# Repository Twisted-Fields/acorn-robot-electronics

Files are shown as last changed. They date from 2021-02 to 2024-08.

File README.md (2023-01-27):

# Acorn Robot Electronics

### About

PCBs designed in Kicad for Acorn the farming robot.

Our dream is that you will fab your own boards, make changes, and share your work - giving this design life beyond our efforts.

Designed by Taylor Alexander for Twisted Fields, for the Acorn Precision Farming Rover.

Many thanks to [Daniel Theobald](https://www.twistedfields.com/blog). Without your financial support and encouragement this project would not have been possible.

Thanks to all of our supporters on Open Collective. Your contributions are helping grow this project in to a sustainable open source organization.

You can support this project yourself at our [Open Collective Page](https://opencollective.com/twisted-fields-research-collective).

To learn more about Acorn, please see our [announcement blog post](https://community.twistedfields.com/t/introducing-acorn-a-precision-farming-rover-from-twisted-fields/).
Or see a more recent [technical update here](https://community.twistedfields.com/t/march-2022-update-simulation-brakes-funding-and-navigation-improvements/202).

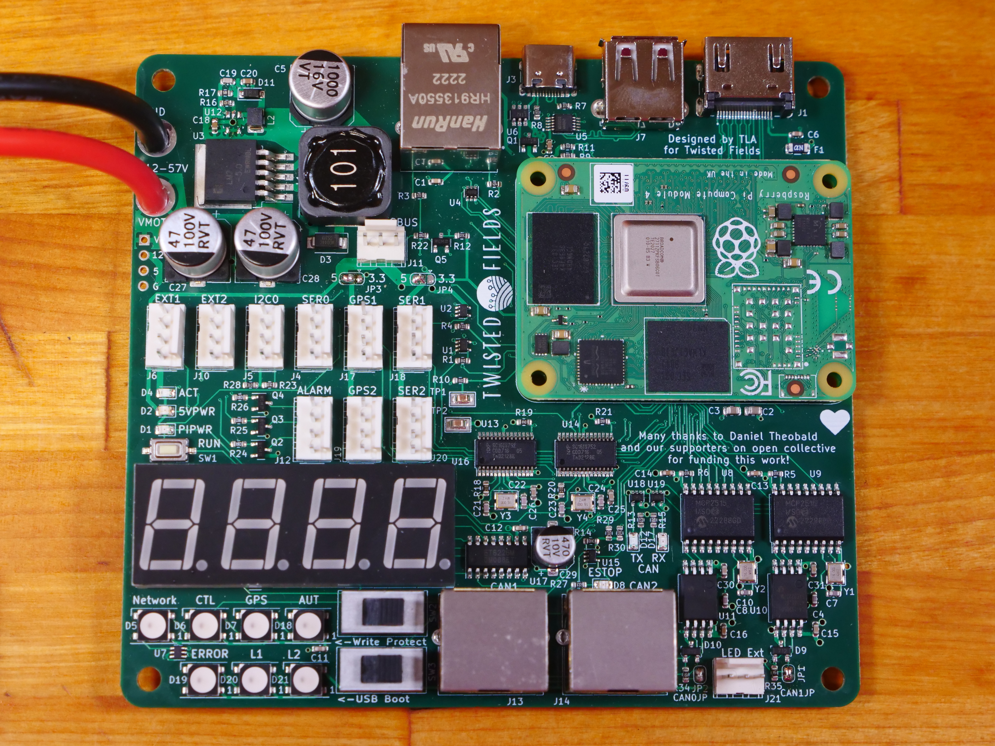
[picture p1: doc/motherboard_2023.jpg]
A photo of the CM4 motherboard


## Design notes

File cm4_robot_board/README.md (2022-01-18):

# Acorn Raspberry Pi Motherboard

### About

This is the motherboard design used on Acorn, the precision farming rover
from Twisted Fields.

This board provides motor control communication to four Odrive motor controllers
via RS-485, e-stop control, motor power control, and more.

For more information please see http://community.twistedfields.com

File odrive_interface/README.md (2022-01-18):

# Acorn Odrive Interface Board

### About

This board attaches to the odrive motor controller and provides
an interface for RS-485 and emergency stop over ethernet cabling.

It also provides connections to a few sensors, and includes
relays for emergency braking.

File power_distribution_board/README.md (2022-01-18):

# Acorn Power Distribution Board

### About

This board attaches to the Acorn motherboard and handles
switching of the high current power going to the motors.

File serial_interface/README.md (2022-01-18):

# Acorn Serial interface board

### About

This board attaches to any raspberry pi 40 pin header
or to the special 40 pin header on our robot motherboard
and provides connections for opto-isolated RS-485 serial
as well as emergency stop connections, designed to
mate with our Odrive interface board.

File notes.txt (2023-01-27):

TODO RECOMMENDATIONS AFTER PRODUCTION

Make clear the polarity for U5 、D19、D5、D6、D20、D7、D21、D18

e-stop should activate if a cable is disconnected. - nevermind, it does this

make CAN controller crystal value more clear - 16mhz not 12mhz!

invert CAN TX/RX LED polarity either by using inverting buffer part number or by rewiring input - maybe inverted is best for fast cut-off?

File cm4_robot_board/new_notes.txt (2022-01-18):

WL_nDisable logic high indicates the enable/disable state of wireless networking. may want to connect it to an LED. can also be pulled low to disable wlan
BT_nDisable same as above for bluetooth

etherney jack for rpi networking
https://www.digikey.com/en/products/detail/bel-fuse-inc/0826-1X1T-GH-F/2257874

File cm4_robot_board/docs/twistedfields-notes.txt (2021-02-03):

CCG304805S or PDQ30-Q48-S5-D for 5v power supply

SC16IS762 in SPI mode for dual serial ports
See this for some background on enabling kernel support.
https://www.raspberrypi.org/forums/viewtopic.php?f=107&t=146908&start=25
Read both pages but check if newer kernels still need this.

Possibly ISL83488 or 65HVD32 or THVD1451 for rs485 line drivers. prefer THVD1451, must double check datasheets if others used.
will use kicad footprint of THVD1451 but may prefer ISL83488 for slew rate limited drivers.
should use 250kbps data rate or lower
See layout guidelines at http://www.ti.com/lit/ds/symlink/thvd1451.pdf

See https://www.waveshare.com/wiki/2-CH_RS485_HAT for some details

Can draw up to 500ma from the 3.3v line on the raspberry pi.
https://pinout.xyz/pinout/pin1_3v3_power

Should add a connector for SPI e-ink display.
https://www.waveshare.com/wiki/7.5inch_e-Paper_HAT_(B)

ABM3C-14.7456MHZ-D4Y-T  for serial crystal

BTS500851TMAATMA1 for power switch.

zener  	MMSZ5226B-7-F 

Power Capacitors
565-4013-ND 
EKYB101ELL101MJ20S 

Inductor
RLB0913-470K-ND 
RLB0913-470K 

THVD1451 RS485 tranceiver

TVS Diodes:
SM712-TP or
SM712-02HTG 

Solar current sensor:
unidirectional 10A
ACS725LLCTR-10AU-T

Bidirectional 5A:
ACS722LLCTR-05AB-T

Bidirectional 10A:
ACS722LLCTR-10AB-T

Slide switchs should be:
ASE1D-2M-10-Z
Kicad lists another part for the footprint, but they match. This part is 60v tolerant.

SPST switch:
GF-123-0054

alarm
TXL7-V96-930-S

Molex connectors for keypad:
0022232051 

inductor:
MLZ2012N100LT000

5v external power supplies for Jetson Nano:
$108 compact 100w:
https://www.digikey.com/product-detail/en/cui-inc/PQA50-D48-S5-T/102-3295-ND/4765796
$39 60w no remote on/off (can drive from switched 48v):
https://www.digikey.com/product-detail/en/mean-well-usa-inc/RSD-60L-5/1866-5467-ND/7706269
$40 compact 30w:
https://www.digikey.com/product-detail/en/cui-inc/PYBE30-Q48-S5-DIN/102-6035-ND/9859991

e-paper screen wiring:
https://www.waveshare.com/wiki/7.5inch_e-Paper_HAT_(B)

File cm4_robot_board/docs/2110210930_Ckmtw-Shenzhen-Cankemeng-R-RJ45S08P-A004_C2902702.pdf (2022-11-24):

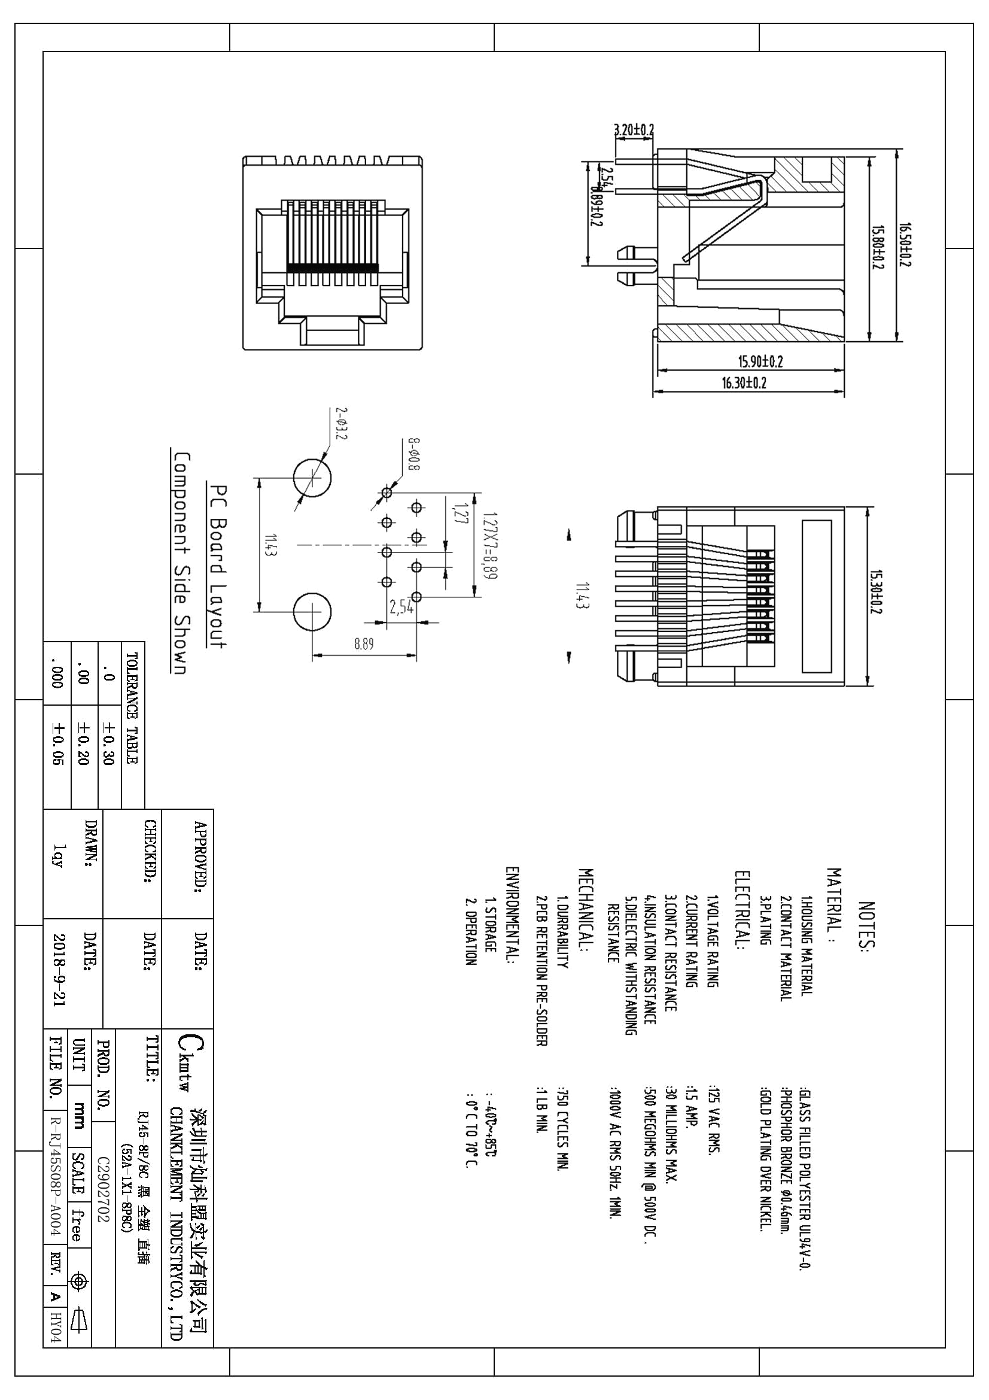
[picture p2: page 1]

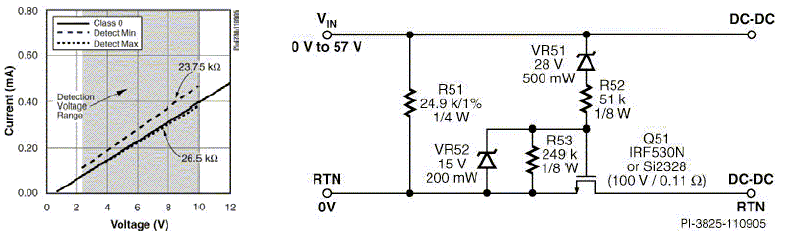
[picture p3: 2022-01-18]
cm4_robot_board/docs/poe/class_0_via_eetimes.gif

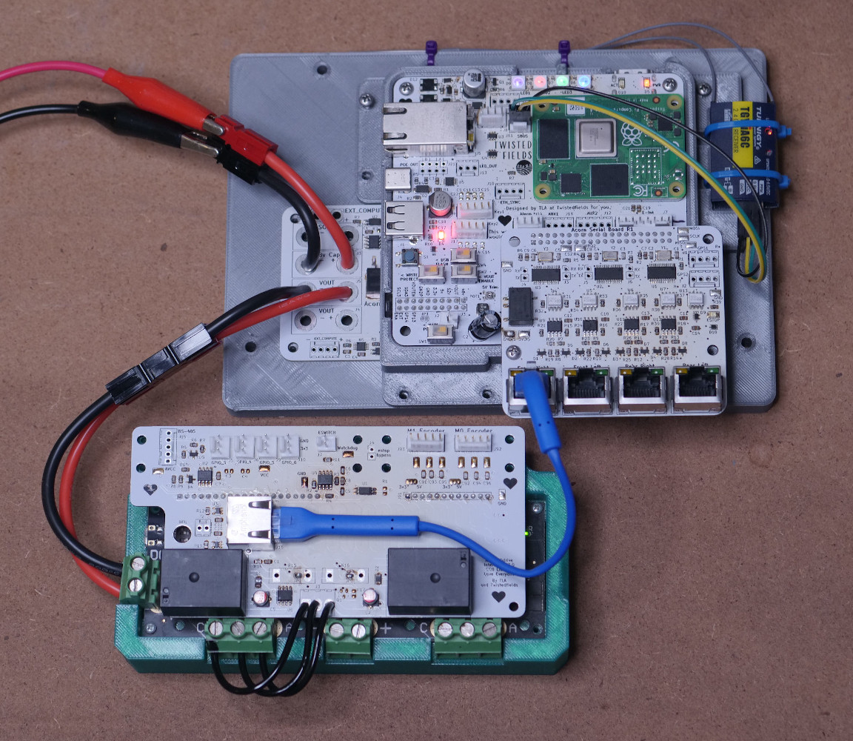
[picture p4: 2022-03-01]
doc/motherboard_all.jpg

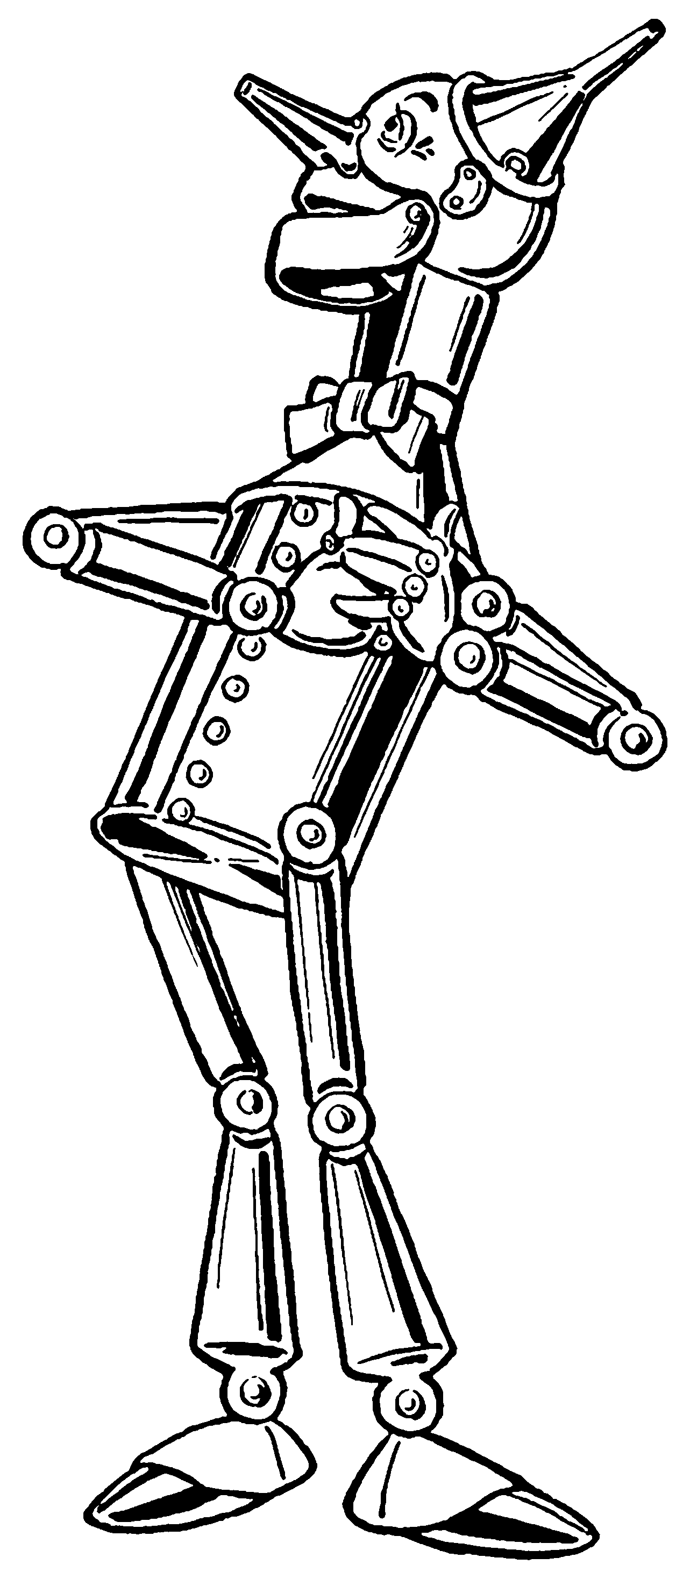
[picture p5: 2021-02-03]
cm4_robot_board/artwork/Tin_Woodman.png

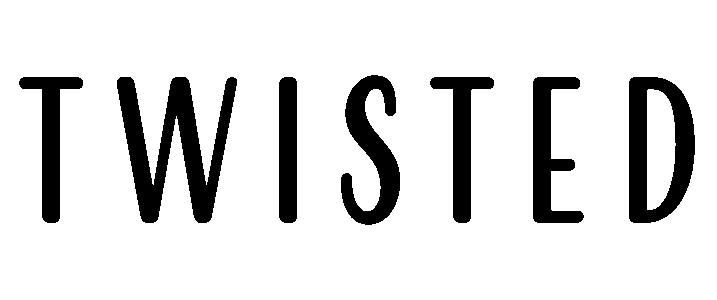
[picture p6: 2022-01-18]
cm4_robot_board/artwork/twisted.png

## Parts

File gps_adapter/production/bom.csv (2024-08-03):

Designator | Footprint | Quantity | Value | LCSC Part #
H1, H2, H3, H4 | MountingHole_3.7mm | 4 | MountingHole
J3 | PinHeader_2x05_P2.54mm_Vertical | 1 | Serial Input
JP1, JP2 | SolderJumper-2_P1.3mm_Open_RoundedPad1.0x1.5mm | 2 | SolderJumper_2_Open
U1, U2 | GPS-RTK-SMA | 2 | GPS-RTK-SMA

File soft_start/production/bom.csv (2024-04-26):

Designator | Footprint | Quantity | Value | LCSC Part #
C1, C2 | 0603 | 2 | 20p | C1648
C14, C15, C29, C30, C31, C33, C34, C35, C36, C37, C4 | 0603 | 11 | 100n | C14663
C16, C32 | 0603 | 2 | 1u | C15849
C3 | 0805 | 1 | 10u | C15850
C5, C7 | 1210 | 2 | 4.7uF 100V | C342614
C6 | CP_Elec_8x10.5 | 1 | 47uF 63V solid | C5246568
D1 | D_SMA | 1 | SS310 | C15874
D2, D33 | D_SOD-323 | 2 | Zener 10v | C85383
D28, D29 | D_SOD-323 | 2 | 1N4148WS | C2128
J2 | Ckmtw-W-2510S06P_1x06_P2.54mm_Vertical | 1 | Conn_01x06 | C140771
J3 | PowerPole_PP45_1336G1_1x2_Horizontal | 1 | Power Output
J4, J5 | PowerPole_PP45_1336G1_1x2_Horizontal | 2 | Conn_01x02
L3 | L_Chilisin_BMRB00060612 | 1 | 47uH | C5189962
Q1, Q2 | SOT-23 | 2 | Q_NMOS_GSD | C2891566
Q3, Q4, Q5, Q6 | TO-252-2 | 4 | 100V 34A PMOS | C2758447
R1, R2 | 1206 | 2 | 10k | C3013377
R13, R15 | 2512 | 2 | 3mΩ | C2688862
R3, R40 | 2512 | 2 | 2k 2 watt | C175463
R34, R35, R37, R38 | 0603 | 4 | 50k 0.1% | C304067
R36, R39 | 0603 | 2 | 5.1k 0.1% | C122969
R8 | 0603 | 1 | 1.1k | C22764
TP1 | TestPoint_Loop_D2.60mm_Drill1.6mm_Beaded | 1 | TestPoint | C5199814
U1 | SOT-23-6 | 1 | USBLC6-4SC6 | C558419
U2 | SOIC-8_5.23x5.23mm_P1.27mm | 1 | W25Q128JVSIQ | C113767
U3 | SOT-223-3_TabPin2 | 1 | LD1117S33TR_SOT223 | C2845050
U4 | RP2040-QFN-56 | 1 | RP2040 | C2040
U7 | SOT-23-6 | 1 | INA181A2 | C2058784
Y1 | Crystal_SMD_3225-4Pin_3.2x2.5mm | 1 | 12MHz | C9002

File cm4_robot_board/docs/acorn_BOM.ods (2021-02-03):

Reference | Quantity | Value | Digikey | Footprint | Datasheet | Field4 | Field5 | Category | DK_Datasheet_Link | DK_Detail_Page | Description | Family | MPN | Manufacturer | Status | Digi-Key_PN | Field6
C18 | 1 | 1000pF | 311-1469-1-ND | Capacitor_SMD:C_0805_2012Metric | ~
C2 C1 C9 C8 | 4 | 18pF | 311-1102-1-ND | Capacitor_SMD:C_0805_2012Metric | ~
C20 | 1 | 0.15uF | 311-3393-1-ND | Capacitor_SMD:C_0805_2012Metric | ~
C27 C25 C23 C21 C28 C26 C24 C22 | 8 | DNP |  | Capacitor_SMD:C_0805_2012Metric | ~
C3 | 1 | 1uF 100v | 490-10918-1-ND | Capacitor_SMD:C_0805_2012Metric | ~
C4 | 1 | CP | 565-4013-ND | Capacitor_THT:CP_Radial_D10.0mm_P5.00mm | ~
C5 C7 C6 C13 C16 C15 C11 C12 C17 C19 C14 C10 | 12 | 0.1uF | 311-1361-1-ND | Capacitor_SMD:C_0805_2012Metric | ~
C99 | 1 | 150pF | 399-8024-1-ND | Capacitor_SMD:C_0805_2012Metric | ~
D1 D3 D14 D16 | 4 | LED_GREEN | 404-1046-1-ND | LED_SMD:LED_1206_3216Metric | ~
D12 D10 D13 D11 D23 D21 D24 D22 | 8 | CDSOT23-SM712 | CDSOT23-SM712CT-ND | digikey-footprints:SOT-23-3 | https://www.bourns.com/docs/Product-Datasheets/CDSOT23-SM712.pdf
D18 D25 D20 D19 | 4 | 3.3v Zener | MMSZ5226B-FDITR-ND | Diode_SMD:D_SOD-123 | ~
D2 D4 D15 D17 | 4 | LED_ORANGE | 404-1234-1-ND | LED_SMD:LED_1206_3216Metric | ~
D26 | 1 | LED | 160-1643-1-ND | LED_SMD:LED_1206_3216Metric | ~
D7 D6 D5 | 3 | D | MMSD4148T1GOSCT-ND | Diode_SMD:D_SOD-123 | ~
D8 | 1 | 12v Zener | MMSZ5242B-TPMSCT-ND | Diode_SMD:D_SOD-123 | ~
D9 | 1 | LED_RED | 404-1042-1-ND | LED_SMD:LED_1206_3216Metric | ~
H1 H3 H4 H2 | 4 | MountingHole |  | MountingHole:MountingHole_3.7mm | ~
J10 | 1 | Raspberry Pi | 1690-RASPBERRYPI4B/4GB-ND | Connector_PinHeader_2.54mm:PinHeader_2x20_P2.54mm_Vertical
J11 | 1 | Conn_01x06 |  | Connector_PinHeader_2.54mm:PinHeader_1x06_P2.54mm_Vertical | ~
J13 J14 J26 J27 J23 | 5 | Conn_01x05 | 455-1707-ND | Connector_JST:JST_PH_B5B-PH-K_1x05_P2.00mm_Vertical | ~ |  |  | Discrete Semiconductor Products | https://www.onsemi.com/pub/Collateral/NDS7002A-D.PDF | /product-detail/en/on-semiconductor/2N7002/2N7002NCT-ND/244664 | MOSFET N-CH 60V 115MA SOT-23 | Transistors - FETs, MOSFETs - Single | 2N7002 | ON Semiconductor | Active
J16 | 1 | Conn_01x08 | 455-1710-ND | Connector_JST:JST_PH_B8B-PH-K_1x08_P2.00mm_Vertical | ~ |  |  | Circuit Protection | https://www.bourns.com/docs/Product-Datasheets/CDSOT23-SM712.pdf | /product-detail/en/bourns-inc/CDSOT23-SM712/CDSOT23-SM712CT-ND/1630607 | TVS DIODE 7V/12V 14V/26V SOT23-3 | TVS - Diodes | CDSOT23-SM712 | Bourns Inc. | Active
J19 J25 J12 J15 J30 J18 | 6 | Conn_01x04 | 455-1706-ND | Connector_JST:JST_PH_B4B-PH-K_1x04_P2.00mm_Vertical | ~ |  |  | Discrete Semiconductor Products | http://aosmd.com/res/data_sheets/AO3401A.pdf | /product-detail/en/alpha-omega-semiconductor-inc/AO3401A/785-1001-1-ND/1855943 | MOSFET P-CH 30V 4A SOT23 | Transistors - FETs, MOSFETs - Single | AO3401A | Alpha & Omega Semiconductor Inc. | Active
J20 J24 | 2 | Conn_01x03 | 455-1705-ND | Connector_JST:JST_PH_B3B-PH-K_1x03_P2.00mm_Vertical | ~
J28 J29 | 2 | Conn_01x05 | WM4203-ND | Connector_Molex:Molex_KK-254_AE-6410-05A_1x05_P2.54mm_Vertical | 22232051 |  |  | Potentiometers, Variable Resistors | https://www.bourns.com/docs/Product-Datasheets/TC33.pdf | /product-detail/en/bourns-inc/TC33X-2-103E/TC33X-103ETR-ND/612858 | TRIMMER 10K OHM 0.1W J LEAD TOP | Trimmer Potentiometers | TC33X-2-103E | Bourns Inc. | Active
J3 J2 | 2 | Conn_01x02 | 455-1704-ND | Connector_JST:JST_PH_B2B-PH-K_1x02_P2.00mm_Vertical | ~
J32 | 1 | Conn_01x02 | 455-1611-ND | Connector_JST:JST_EH_B2B-EH-A_1x02_P2.50mm_Vertical | ~
J4 J5 J6 J1 | 4 | Conn_01x02 |  | twisted_library:BigWirePads | ~
J9 J21 J22 J8 J7 J17 J31 | 7 | Conn_01x02 |  | Connector_PinHeader_2.54mm:PinHeader_1x02_P2.54mm_Vertical | ~
L1 | 1 | L | RLB0913-470K-ND | Inductor_THT:L_Radial_D8.7mm_P5.00mm_Fastron_07HCP | ~
L2 | 1 | 10uH | 445-6762-1-ND | Inductor_SMD:L_0805_2012Metric | MLZ2012N100LT000
POT1 | 1 | TC33X-2-103E | TC33X-103ETR-ND | digikey-footprints:Trimpot_3.8mmx3.6mm_TC33X-2-103E | https://www.bourns.com/docs/Product-Datasheets/TC33.pdf
PS1 | 1 | SPBW06F-12 | 1866-4811-ND | library:CONV_SPBW06F-12 | Manufacturer Recommendations
Q12 | 1 | AO3401A | FDN352APCT-ND | digikey-footprints:SOT-23-3 | http://aosmd.com/res/data_sheets/AO3401A.pdf
Q3 Q13 Q10 Q8 Q7 Q6 Q1 Q2 Q11 Q9 Q4 | 11 | 2N7002 | 2N7002NCT-ND | digikey-footprints:SOT-23-3 | https://www.onsemi.com/pub/Collateral/NDS7002A-D.PDF | CUI Inc | Manufacturer Recommendations
Q5 | 1 | FDMS8050 | BSC030N08NS5ATMA1CT-ND | Package_TO_SOT_SMD:TDSON-8-1 | https://www.fairchildsemi.com/datasheets/FD/FDMS8050.pdf | MEANWELL | 11.1mm |  |  |  |  |  |  |  |  |  | N/A
R11 R69 R72 R56 R39 R37 R1 R10 R12 R73 R70 R68 R29 R27 | 14 | 100R | 311-100CRCT-ND | Resistor_SMD:R_0805_2012Metric | ~
R13 R41 | 2 | 330R | A106061CT-ND | Resistor_SMD:R_0805_2012Metric | ~
R14 R74 | 2 | 220R | A129741CT-ND | Resistor_SMD:R_0805_2012Metric | ~
R15 R22 R17 R25 R44 R51 R46 R54 | 8 | 130R | RMCF0805FT130RCT-ND | Resistor_SMD:R_0805_2012Metric | ~
R19 R16 R21 R23 R20 R18 R24 R26 R48 R45 R50 R52 R49 R47 R53 R55 | 16 | 750R | RMCF0805FT750RCT-ND | Resistor_SMD:R_0805_2012Metric | ~
R2 R3 R4 R5 R30 R31 R32 R33 | 8 | 499R | 311-499CRCT-ND | Resistor_SMD:R_0805_2012Metric | ~
R36 | 1 | 10K | 311-10.0KCRCT-ND | Resistor_SMD:R_0805_2012Metric | ~
R42 | 1 | 44.2k 0.1% | P44.2KDACT-ND | Resistor_SMD:R_0805_2012Metric | ~
R43 R61 | 2 | 10.2k 0.1% | P10.2KDACT-ND | Resistor_SMD:R_0805_2012Metric | ~
R58 | 1 | DNP |  | Resistor_SMD:R_0805_2012Metric | ~
R60 R65 | 2 | 100K 0.1% | P100KDACT-ND | Resistor_SMD:R_0805_2012Metric | ~
R66 | 1 | 6.49k 0.1% | A103685CT-ND | Resistor_SMD:R_0805_2012Metric | ~
R67 | 1 | DNS for ACS725 / 0R for ACS722 | 311-0.0ARCT-ND | Resistor_SMD:R_0805_2012Metric | ~
R7 R34 R71 R59 R62 | 5 | 10K | 311-10.0KCRCT-ND | Resistor_SMD:R_0805_2012Metric | ~
R8 R35 R38 R63 R57 R40 R6 R64 R28 | 9 | 1k | 311-1.0KARCT-ND | Resistor_SMD:R_0805_2012Metric | ~
SW2 SW1 | 2 | SW_SPDT | 563-1151-ND | digikey-footprints:Switch_Slide_11.6x4mm_EG1218 | ~
TH1 | 1 | Thermistor | BC2733CT-ND | Resistor_SMD:R_0805_2012Metric | ~
TP3 TP4 TP5 TP6 TP7 TP2 TP1 | 7 | TestPoint | 36-5015CT-ND | TestPoint:TestPoint_Keystone_5015_Micro-Minature | ~
U1 U2 U3 | 3 | BTS50085-1TMA | BTS500851TMAATMA1CT-ND | Package_TO_SOT_SMD:TO-263-7_TabPin4 | https://www.infineon.com/dgdl/Infineon-BTS50085-1TMA-DS-v01_00-EN.pdf?fileId=5546d4625a888733015aa435bccd114b
U10 | 1 | HDC1080 | 296-46272-1-ND | Package_SON:Texas_PWSON-N6 | http://www.ti.com/lit/ds/symlink/hdc1080.pdf
U14 | 1 | ACS725xLCTR-10AU | 620-1634-1-ND | Package_SO:SOIC-8_3.9x4.9mm_P1.27mm | http://www.allegromicro.com/~/media/Files/Datasheets/ACS725-Datasheet.ashx?la=en
U15 | 1 | MCP23017_SS | MCP23017T-E/SSTR-ND | Package_SO:SSOP-28_5.3x10.2mm_P0.65mm | http://ww1.microchip.com/downloads/en/DeviceDoc/20001952C.pdf
U4 | 1 | PDQ30-Q48-S5-D | 102-3897-ND | library:CONV_PDQ30-Q48-S5-D | 1
U5 U11 | 2 | SC16IS752 | 568-4021-5-ND | Package_SO:TSSOP-28_4.4x9.7mm_P0.65mm | DOCUMENTATION
U6 U7 U13 U12 | 4 | THVD1451D | 296-THVD1451D-ND | Package_SO:SOIC-8_3.9x4.9mm_P1.27mm | http://www.ti.com/lit/ds/symlink/thvd1451.pdf
U8 U9 | 2 | ADS1115IDGS | 296-38849-1-ND | Package_SO:TSSOP-10_3x3mm_P0.5mm | http://www.ti.com/lit/ds/symlink/ads1113.pdf
Y1 Y2 | 2 | Crystal_GND24 | 535-11286-1-ND | Crystal:Crystal_SMD_Abracon_ABM3C-4Pin_5.0x3.2mm | ~

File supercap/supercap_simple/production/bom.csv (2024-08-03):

Designator | Footprint | Quantity | Value | LCSC Part #
C10, C11, C12, C13, C17, C18, C19, C20, C21, C22, C23, C24, C25, C26, C27, C5, C6, C7, C8, C9 | CP_Radial_D18.0mm_P7.50mm | 20 | 120F 2.3v
D10, D11, D12, D13, D14, D15, D16, D17, D18, D19, D2, D20, D21, D3, D4, D5, D6, D7, D8, D9 | DIO_PESD5V0S1UL_315 | 20 | 2.4v zener | C551192
J1, J2, J4, J5 | PowerPole_PP45_1336G1_1x2_Horizontal | 4 | Conn_01x02
J3 | AMASS_XT30PW-M_1x02_P2.50mm_Horizontal | 1 | XT30PW-M | C431092
J6 | AMASS_XT30PW-F_1x02_P2.50mm_Horizontal | 1 | XT30PW-F20.G.Y | C2913282

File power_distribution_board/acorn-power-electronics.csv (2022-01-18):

Collated Components:
Item | Qty | Reference(s) | Value | LibPart | Footprint | Datasheet | AVAILABILITY | DESCRIPTION | Digikey | MF | MP | MPN | PACKAGE | PRICE
1 | 2 | C1, C4 | 0.1uF | Device:C | Capacitor_SMD:C_0805_2012Metric | ~ |  |  | 311-1361-1-ND
2 | 1 | C2 | 1000pF | Device:C | Capacitor_SMD:C_0805_2012Metric | ~ |  |  | 311-1469-1-ND
3 | 1 | C3 | 0.15uF | Device:C | Capacitor_SMD:C_0805_2012Metric | ~ |  |  | 311-3393-1-ND
4 | 2 | D1, D2 | BZX84Cxx | Diode:BZX84Cxx | Diode_SMD:D_SOT-23_ANK | https://diotec.com/tl_files/diotec/files/pdf/datasheets/bzx84c2v4.pdf |  |  | MMBZ5240B-FDICT-ND |  |  | MMBZ5240B-7-F
5 | 1 | J1 | Conn_01x04 | Connector_Generic:Conn_01x04 | Connector_Molex:Molex_KK-254_AE-6410-04A_1x04_P2.54mm_Vertical | ~ |  |  | WM4202-ND |  |  | 0022232041
6 | 1 | J7 | Conn_02x10_Counter_Clockwise | Connector_Generic:Conn_02x10_Odd_Even | Connector_PinHeader_2.54mm:PinHeader_2x10_P2.54mm_Vertical | ~ |  |  | S9197-ND |  |  | SFH11-PBPC-D10-ST-BK
7 | 1 | Q1 | IXTA96P085T-TRL | :P_CHANNEL_1 | taylor_footprints:TO-263-2-pad4 | https://www.vishay.com/docs/69253/sud19p06.pdf |  |  | IXTA96P085T-TRLCT-ND |  |  | IXTA96P085T-TRL
8 | 1 | Q2 | IXTA96P085T-TRL | :P_CHANNEL_2 | taylor_footprints:TO-263-2-pad4 | https://www.vishay.com/docs/69253/sud19p06.pdf |  |  | IXTA96P085T-TRLCT-ND |  |  | IXTA96P085T-TRL
9 | 1 | Q3 | IXTA96P085T-TRL | taylor_kicad:P_CHANNEL | taylor_footprints:TO-263-2-pad4 | https://www.vishay.com/docs/69253/sud19p06.pdf |  |  | IXTA96P085T-TRLCT-ND |  |  | IXTA96P085T-TRL
10 | 1 | Q4 | IXTA96P085T-TRL | :P_CHANNEL_3 | taylor_footprints:TO-263-2-pad4 | https://www.vishay.com/docs/69253/sud19p06.pdf |  |  | IXTA96P085T-TRLCT-ND |  |  | IXTA96P085T-TRL
11 | 2 | R1, R2 | 330R | Device:R | Resistor_SMD:R_0805_2012Metric | ~ |  |  | A106061CT-ND
12 | 2 | R3, R5 | 200 | Device:R | Resistor_SMD:R_0805_2012Metric | ~ |  |  | 311-200ARCT-ND
13 | 3 | R4, R6, R8 | 1k | Device:R | Resistor_SMD:R_0805_2012Metric | ~ |  |  | 311-1.0KARCT-ND |  |  | RC0805FR-071KL
14 | 1 | R7 | DNS for ACS725 / 0R for ACS722 | Device:R | Resistor_SMD:R_0805_2012Metric | ~ |  |  | 311-0.0ARCT-ND
15 | 2 | U1, U2 | ACPL-214-500E | Isolator:ACPL-214-500E | Package_SO:SOP-4_4.4x2.6mm_P1.27mm | https://docs.broadcom.com/doc/AV02-0469EN |  |  | 559-1105-ND |  |  | PS2805A-1-A
16 | 1 | U3 | ACS725xLCTR-10AU | Sensor_Current:ACS725xLCTR-10AU | Package_SO:SOIC-8_3.9x4.9mm_P1.27mm | http://www.allegromicro.com/~/media/Files/Datasheets/ACS725-Datasheet.ashx?la=en |  |  | 620-1719-1-ND |  |  | ACS724LLCTR-10AB-T
17 | 1 | U4 | PDS1-S5-S12-M-TR | PDS1-S3-S3-M:PDS1-S3-S3-M | CONV_PDS1-S3-S3-M |  | Bad | DC DC CONVERTER 12V 1W | 102-2686-1-ND | CUI | PDS1-S12-S12-M | PDS1-S5-S12-M-TR | SMD-8 CUI | 4.02 USD
18 | 1 | U5 | ADS1115IDGS | Analog_ADC:ADS1115IDGS | Package_SO:TSSOP-10_3x3mm_P0.5mm | http://www.ti.com/lit/ds/symlink/ads1113.pdf |  |  | 296-25226-1-ND |  |  | ADS1014IDGST

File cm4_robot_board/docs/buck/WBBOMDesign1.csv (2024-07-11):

Part | Manufacturer | Part Number | Quantity | Price ($) | Footprint (mm²) | Description
Cout | MuRata | GRM32ER61C476KE15L | 2 | 0.17 | 14.7 | Cap: 47 µF Total Derated Cap: 63 µF VDC: 16 V ESR: 3.04 mΩ Package: 1210
Ccomp2 | Johanson Technology | 250R07N151JV4T | 1 | 0.01 | 3 | Cap: 150 pF Total Derated Cap: 150 pF VDC: 25 V ESR: 0 Ω Package: 0402
Rcomp | Vishay-Dale | CRCW040230K9FKED | 1 | 0.01 | 3 | Resistance: 30.9 kΩ Tolerance: 1.0% Power: 63 mW
Rt | Vishay-Dale | CRCW040247K5FKED | 1 | 0.01 | 3 | Resistance: 47.5 kΩ Tolerance: 1.0% Power: 63 mW
U1 | Texas Instruments | LM5116MH/NOPB | 1 | 2.812 | 71.4
Cramp | Samsung Electro-Mechanics | CL10C152JB8NNNC | 1 | 0.02 | 4.68 | Cap: 1.5 nF Total Derated Cap: 1.5 nF VDC: 50 V ESR: 0 Ω Package: 0603
Ruv1 | Vishay-Dale | CRCW080532K4FKEA | 1 | 0.01 | 6.75 | Resistance: 32.4 kΩ Tolerance: 1.0% Power: 125 mW
L1 | Vishay-Dale | IHLP6767GZER560M11 | 1 | 2.32 | 366.72 | L: 56 µH DCR: 57.8 mΩ IDC: 4.2 A
Ccomp | TDK | C1608C0G1H472J080AA | 1 | 0.04 | 4.68 | Cap: 4.7 nF Total Derated Cap: 4.7 nF VDC: 50 V ESR: 0 Ω Package: 0603
Renable | Vishay-Dale | CRCW04021M00FKED | 1 | 0.01 | 3 | Resistance: 1 MΩ Tolerance: 1.0% Power: 63 mW
Cvcc | Taiyo Yuden | TMK212BJ105KG-T | 1 | 0.03 | 6.75 | Cap: 1 µF Total Derated Cap: 1 µF VDC: 25 V ESR: 1 mΩ Package: 0805
M1 | Infineon Technologies | BSC320N20NS3 G | 1 | 1.78 | 55.13 | VdsMax: 200 V IdsMax: 36 Amps
Ruv2 | Vishay-Dale | CRCW0805110KFKEA | 1 | 0.01 | 6.75 | Resistance: 110 kΩ Tolerance: 1.0% Power: 125 mW
D1 | Nexperia | BAS516 115 | 1 | 0.22 | 5.13 | Type: Switching VRRM: 100 V Io: 250 mA
Cboot | AVX | 08053C104KAT2A | 1 | 0.01 | 6.75 | Cap: 100 nF Total Derated Cap: 100 nF VDC: 25 V ESR: 280 mΩ Package: 0805
Css | TDK | CGA4J2C0G1H333J125AA | 1 | 0.08 | 6.75 | Cap: 33 nF Total Derated Cap: 33 nF VDC: 50 V ESR: 0 Ω Package: 0805
Cinx | TDK | C2012X7T2E104K125AA | 1 | 0.09 | 6.75 | Cap: 100 nF Total Derated Cap: 100 nF VDC: 250 V ESR: 1 mΩ Package: 0805
Rfbb | Yageo | RT0805BRD0710K4L | 1 | 0.054 | 6.75 | Resistance: 10.4 kΩ Tolerance: 0.1% Power: 125 mW
Rfbt | Panasonic | ERJ-6ENF3242V | 1 | 0.01 | 6.75 | Resistance: 32.4 kΩ Tolerance: 1.0% Power: 125 mW
Cin | CUSTOM | CUSTOM | 1 | NA | NA | Cap: 2.2 µF Total Derated Cap: 2.2 µF VDC: 125 V ESR: 1 µΩ Package: null
Rsense | Stackpole Electronics Inc | CSR1206FK20L0 | 1 | 0.1 | 10.92 | Resistance: 20 mΩ Tolerance: 1.0% Power: 500 mW
M2 | Infineon Technologies | IPW60R199CPFKSA1 | 2 | 4.42 | 123.2 | VdsMax: 600 V IdsMax: 32 Amps

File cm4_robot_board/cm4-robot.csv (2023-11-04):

Comment | Designator | Footprint | LCSC
0.1uF | C1,C6,C9,C11,C12,C13,C14,C15,C16,C25,C26,C30,C31 | Capacitor_SMD:C_0603_1608Metric | C14663
4.7uF | C18 | Capacitor_SMD:C_0603_1608Metric | C69335
2.7pF | C19 | Capacitor_SMD:C_0603_1608Metric | C95180
10uF | C2,C3 | Capacitor_SMD:C_0805_2012Metric | C15850
1uF | C20 | Capacitor_SMD:C_0603_1608Metric | C59302
22p | C21,C22,C23,C24 | Capacitor_SMD:C_0603_1608Metric | C1653
47uF | C27,C28 | Capacitor_SMD:CP_Elec_10x10 | C335988
470uF 10V | C29 | Capacitor_SMD:CP_Elec_6.3x7.7 | C335982
18p | C4,C7,C8,C10 | Capacitor_SMD:C_0603_1608Metric | C1647
1000uF | C5 | Capacitor_SMD:CP_Elec_10x10 | C310843
LED_YELLOW | D1,D17 | LED_SMD:LED_0805_2012Metric | C5137318
MBR0530 | D11 | Diode_SMD:D_SOD-123 | C77336
LED_RED | D2,D8 | LED_SMD:LED_0805_2012Metric | C84256
D_Schottky | D3 | Diode_SMD:D_SMC | C123944
LED_GREEN | D4,D12 | LED_SMD:LED_0805_2012Metric | C5137315
WS2812B | D5,D6,D7,D18,D19,D20,D21 | LED_SMD:LED_WS2812B_PLCC4_5.0x5.0mm_P3.2mm | C2761795
CDSOT23-SM712 | D9,D10 | digikey-footprints:SOT-23-3 | C521963
Polyfuse | F1 | Fuse:Fuse_1206_3216Metric | C70065
1747981-1 | J1 | parts:TE_1747981-1 | C2906135
Conn_01x03 | J11,J21 | Connector_Molex:Molex_KK-254_AE-6410-03A_1x03_P2.54mm_Vertical | C402772
RJ45 | J13,J14 | parts:RJ45_R-RJ45R08P-B000 | C386756
HR913550A | J2 | HANRUN_HR911105A | C163507
Conn_01x01 | J23,J24 | parts:DF40C-100DS-0.4V51 | C424649
USB_C_Receptacle_USB2.0 | J3 | Connector_USB:USB_C_Receptacle_XKB_U262-16XN-4BVC11 | C2835315
Conn_01x04 | J4,J5,J6,J10,J12,J17,J18,J19,J20 | Connector_Molex:Molex_KK-254_AE-6410-04A_1x04_P2.54mm_Vertical | C402777
USB_A | J7 | parts:USB_A_Female_UE27AC54100 | C2345
100uH | L1 | parts:L_15mmx15mm | C970545
10uH | L2 | Inductor_SMD:L_1210_3225Metric | C107341
Q_PMOS_GSD | Q1 | Package_TO_SOT_SMD:SOT-23 | C347476
Q_NMOS_GSD | Q2,Q3,Q4,Q5 | Package_TO_SOT_SMD:SOT-23 | C255584
1k | R1,R10,R19,R21 | Resistor_SMD:R_0603_1608Metric | C21190
27R | R13 | Resistor_SMD:R_0603_1608Metric | C25190
56R | R15 | Resistor_SMD:R_0603_1608Metric | C25196
205k | R16 | Resistor_SMD:R_0603_1608Metric | C22949
1.8M | R17 | Resistor_SMD:R_0603_1608Metric | C177951
10K | R18,R20 | Resistor_SMD:R_0603_1608Metric | C319939
470R | R2,R3 | Resistor_SMD:R_0603_1608Metric | C23179
100R | R22,R24,R25,R26 | Resistor_SMD:R_0603_1608Metric | C105588
120R | R34,R35 | Resistor_SMD:R_0603_1608Metric | C22787
220R | R4,R27 | Resistor_SMD:R_0603_1608Metric | C22962
10k | R5,R6,R12,R14,R23,R28,R29,R30 | Resistor_SMD:R_0603_1608Metric | C25804
5.1k | R7,R8 | Resistor_SMD:R_0603_1608Metric | C23186
2.2k 1% | R9,R11 | Resistor_SMD:R_0603_1608Metric | C4190
B3U-1000P | SW1 | parts:SW_TS_1101_C_W | C318938
SW_SPDT | SW2,SW3 | parts:CS12ANW03 | C319012
TestPoint | TP1,TP2 | TestPoint:TestPoint_Keystone_5019_Minature | C238130
SN74LVC1G07QDCKTQ1 | U1,U2,U15,U18,U19 | Package_TO_SOT_SMD:SOT-353_SC-70-5 | C171458
isolator | U10,U11 | Package_SO:SOIC-8_7.5x5.85mm_P1.27mm | C528763
TPS61040DBVR | U12 | digikey-footprints:SOT-753 | C7722
SC16IS752 | U13,U14 | Package_SO:TSSOP-28_4.4x9.7mm_P0.65mm | C57156
CC56-12SEKWA | U16 | Display_7Segment:CA56-12SEKWA | C54396
ET6226M | U17 | Package_SO:SO-16_3.9x9.9mm_P1.27mm | C347308
LM2576HVS-5 | U3 | Package_TO_SOT_SMD:TO-263-5_TabPin3 | C234209
TPD4E1U06DCKR | U4 | Package_TO_SOT_SMD:SOT-363_SC-70-6 | C194628
ISL54222AIUZ | U5 | parts:ISL54222AIUZ | C231929
LTC4412xS6 | U6 | Package_TO_SOT_SMD:TSOT-23-6 | C514442
TXS0101DCKR | U7 | Package_TO_SOT_SMD:SOT-363_SC-70-6 | C132031
MCP2515-xSO | U8,U9 | Package_SO:SOIC-18W_7.5x11.6mm_P1.27mm | C153782
16MHz | Y1,Y2 | Crystal:Crystal_SMD_3225-4Pin_3.2x2.5mm | C362342
14.7456MHz | Y3,Y4 | Crystal:Crystal_SMD_3225-4Pin_3.2x2.5mm | C2901666

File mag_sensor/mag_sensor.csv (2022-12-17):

Comment | Designator | Footprint | LCSC
10u | C1 | Capacitor_SMD:C_0805_2012Metric | C15850
100n | C2 | Capacitor_SMD:C_0603_1608Metric | C14663
4.7n | C3 | Capacitor_SMD:C_0603_1608Metric | C106218
Conn_01x03 | J1 | Connector_Molex:Molex_KK-254_AE-6410-03A_1x03_P2.54mm_Vertical | C29275
MT9105ET | U1 | Package_TO_SOT_SMD:SOT-23 | C967861

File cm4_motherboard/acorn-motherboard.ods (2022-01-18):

Source: | /home/taylor/pcb/acorn-motherboard/acorn-motherboard.kicad_sch
Date: | Mon 15 Nov 2021 05:38:57 PM PST
Tool: | Eeschema 5.99.0-unknown-47cb7f53fd~143~ubuntu20.04.1
Generator: | /usr/share/kicad-nightly/plugins/bom_csv_grouped_by_value.py
Component Count: | 112
Collated Components:
Item | Qty | Reference(s) | Value | LibPart | Footprint | Datasheet | Category | DK_Datasheet_Link | DK_Detail_Page | Description | Digi-Key_PN | Digikey | Digikey PN | Family | Field4 | Field5 | Field6 | Field7 | Field8 | MPN | Manufacturer | Part Description | Status
1 | 4 | C1, C3, C4, C8 | 0.1uF | Device:C | Capacitor_SMD:C_0805_2012Metric | ~ |  |  |  |  |  | 311-1361-1-ND
2 | 1 | C2 | CP | Device:CP | Capacitor_THT:CP_Radial_D8.0mm_P3.50mm |  |  |  |  |  |  | 1189-1004-ND
3 | 1 | C5 | 22uF | Device:CP | Capacitor_SMD:CP_Elec_8x6.5 |  |  |  |  |  |  | 4447PHCT-ND |  |  |  |  |  |  |  | MAL214699801E3
4 | 2 | C6, C7 | 100n | Device:C | Capacitor_SMD:C_0805_2012Metric | https://search.murata.co.jp/Ceramy/image/img/A01X/G101/ENG/GRM155R71C104KA88-01.pdf |  |  |  |  |  |  |  |  | Farnell | 2611911 | RM EMK105 B7104KV-F | TAIYO YUDEN EUROPE GMBH | 110091611 |  |  | 0.1uF 10% 16V Ceramic Capacitor X7R 0402 (1005 Metric)
5 | 8 | C9, C10, C11, C12, C13, C14, C15, C16 | DNP | Device:C | Capacitor_SMD:C_0805_2012Metric | ~
6 | 4 | C17, C18, C19, C21 | 10uF | Device:C | Capacitor_SMD:C_0805_2012Metric | ~ |  |  |  |  |  | 311-1355-1-ND |  |  |  |  |  |  |  | CC0805ZKY5V6BB106
7 | 2 | C20, C22 | 100uF | Device:C_Polarized | Capacitor_SMD:CP_Elec_8x6.5 | ~ |  |  |  |  |  | 493-9703-1-ND |  |  |  |  |  |  |  | UWF1A101MCL1GS
8 | 1 | C23 | 33pF | Device:C | Capacitor_SMD:C_0805_2012Metric | ~ |  |  |  |  |  | 311-1361-1-ND
9 | 1 | D1 | VTVS58ASMF-HM3-08 | taylor_kicad:tvs_diode | Diode_SMD:D_SMF | https://www.onsemi.com/pub/Collateral/ESD5Z2.5T1-D.PDF | Circuit Protection | https://www.onsemi.com/pub/Collateral/ESD5Z2.5T1-D.PDF | /product-detail/en/on-semiconductor/ESD5Z3.3T1G/ESD5Z3.3T1GOSCT-ND/1967044 | TVS Diode 57.6 volts |  | 112-VTVS58ASMF-HM3-08CT-ND |  | TVS - Diodes |  |  |  |  |  | VTVS58ASMF-HM3-08 | ON Semiconductor |  | Active
10 | 1 | D2 | D | Device:D | taylor_footprints:DO214AC | ~ |  |  |  |  |  | SK32A-LTPMSCT-ND |  |  |  |  |  |  |  | SK32A-LTP
11 | 1 | D3 | D | Device:D | Diode_SMD:D_SMA | ~ |  |  |  |  |  | 112-VSS8D2M10HM3/ICT-ND |  |  |  |  |  |  |  | VSS8D2M10HM3/I
12 | 1 | D4 | LED_RED | Device:LED | LED_SMD:LED_1206_3216Metric | ~ |  |  |  |  |  | 404-1042-1-ND
13 | 1 | D5 | LED_ORANGE | Device:LED | LED_SMD:LED_1206_3216Metric | ~ |  |  |  |  |  | 404-1042-1-ND
14 | 4 | D6, D7, D8, D9 | WS2812B | LED:WS2812B | LED_SMD:LED_WS2812B_PLCC4_5.0x5.0mm_P3.2mm | https://cdn-shop.adafruit.com/datasheets/WS2812B.pdf
15 | 1 | D10 | LED_GREEN | Device:LED | LED_SMD:LED_1206_3216Metric | ~ |  |  |  |  |  | 404-1042-1-ND
16 | 2 | D11, D12 | CD-HD201 | dk_Diodes-Bridge-Rectifiers:CD2320-B11000_Obsolete | taylor_footprints:CD-HD201 | https://media.digikey.com/pdf/Data%20Sheets/Bourns%20PDFs/CD2320-B1.pdf | Discrete Semiconductor Products | https://media.digikey.com/pdf/Data%20Sheets/Bourns%20PDFs/CD2320-B1.pdf | /product-detail/en/bourns-inc/CD2320-B11000/CD2320-B11000CT-ND/3741943 | BRIDGE RECT 1PHASE 1KV 1A 2320 |  | CD-HD201CT-ND |  | Diodes - Bridge Rectifiers |  |  |  |  |  | CD2320-B11000 | Bourns Inc. |  | Obsolete NonStock
17 | 5 | H1, H2, H3, H4, H5 | MountingHole | Mechanical:MountingHole | MountingHole:MountingHole_3.7mm | ~
18 | 1 | J1 | USB_A | taylor_kicad:USB_A | digikey-footprints:USB_A_Female_UE27AC54100 | ~ |  |  |  |  |  | UE27AC54100-ND |  |  |  |  |  |  |  | UE27AC54100
19 | 1 | J2 | Conn_01x02 | Connector_Generic:Conn_01x02 | Connector_Molex:Molex_KK-254_AE-6410-02A_1x02_P2.54mm_Vertical | ~ |  |  |  |  |  | 455-1704-ND
20 | 1 | J3 | Conn_02x10_Counter_Clockwise | Connector_Generic:Conn_02x10_Odd_Even | Connector_PinHeader_2.54mm:PinHeader_2x10_P2.54mm_Vertical | ~
21 | 1 | J4 | USB_C_Receptacle_USB2.0 | Connector:USB_C_Receptacle_USB2.0 | Connector_USB:USB_C_Receptacle_GCT_USB4085 | https://www.usb.org/sites/default/files/documents/usb_type-c.zip |  |  |  |  |  | 2073-USB4085-GF-ACT-ND |  |  |  |  |  |  |  | USB4085-GF-A
22 | 1 | J5 | 0826-1X1T-GH-F | 2021-10-21_03-20-16:0826-1X1T-GH-F | footprints6:0826-1X1T-GH-F
23 | 1 | J6 | Raspberry_Pi_2_3 | Connector:Raspberry_Pi_2_3 | Connector_PinSocket_2.54mm:PinSocket_2x20_P2.54mm_Vertical | https://www.raspberrypi.org/documentation/hardware/raspberrypi/schematics/rpi_SCH_3bplus_1p0_reduced.pdf
24 | 1 | J7 | Conn_01x08 | Connector_Generic:Conn_01x08 | Connector_Molex:Molex_KK-254_AE-6410-08A_1x08_P2.54mm_Vertical | ~ |  |  |  |  |  | 455-1710-ND
25 | 5 | J8, J9, J10, J14, J18 | Conn_01x04 | Connector_Generic:Conn_01x04 | Connector_Molex:Molex_KK-254_AE-6410-04A_1x04_P2.54mm_Vertical | ~ |  |  |  |  |  | 455-1706-ND
26 | 2 | J11, J13 | Conn_01x03 | Connector_Generic:Conn_01x03 | Connector_Molex:Molex_KK-254_AE-6410-03A_1x03_P2.54mm_Vertical | ~
27 | 3 | J12, J16, J17 | Conn_01x05 | Connector_Generic:Conn_01x05 | Connector_Molex:Molex_KK-254_AE-6410-05A_1x05_P2.54mm_Vertical | ~ |  |  |  |  |  | 455-1707-ND
28 | 1 | J15 | 690-019-298-412 | CM4IO:HDMI_A_1.4 | CM4IO:EDAC 690-019-298-412 | https://www.tme.eu/Document/f15dffbcfad8545e17826f72d36911c8/206A-SEAN-R03.pdf |  |  |  |  |  |  |  |  | Farnell | 2614936 | 690-019-298-412 | EDAC | UCON00802 |  |  | HDMI Connector, Right Angle, 19 Contacts, Receptacle, Surface Mount, Surface Mount Right Angle
29 | 2 | J19, J20 | Conn_01x22_Female | Connector:Conn_01x22_Female | Connector_FFC-FPC:Hirose_FH12-22S-0.5SH_1x22-1MP_P0.50mm_Horizontal | https://www.hirose.com/product/document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 |  |  |  |  |  |  |  |  | Mouser | 798-FH12-22S-0.5SH55 | FH12-22S-0.5SH55 | Hirose |  |  |  | 22 Position FFC, FPC Connector Contacts, Bottom 0.020" (0.50mm) Surface Mount, Right Angle
30 | 1 | JP1 | Jumper_2_Open | Jumper:Jumper_2_Open | Jumper:SolderJumper-2_P1.3mm_Open_RoundedPad1.0x1.5mm | ~
31 | 1 | L1 | L | Device:L | inductor_power:VLCF4028T-1R2N2R7-2 | ~ |  |  |  |  |  | 445-6544-1-ND
32 | 1 | POT1 | TC33X-2-103E | dk_Trimmer-Potentiometers:TC33X-2-103E | digikey-footprints:Trimpot_3.8mmx3.6mm_TC33X-2-103E | https://www.bourns.com/docs/Product-Datasheets/TC33.pdf | Potentiometers, Variable Resistors | https://www.bourns.com/docs/Product-Datasheets/TC33.pdf | /product-detail/en/bourns-inc/TC33X-2-103E/TC33X-103ETR-ND/612858 | TRIMMER 10K OHM 0.1W J LEAD TOP |  | TC33X-103ECT-ND‎ |  | Trimmer Potentiometers |  |  |  |  |  | TC33X-2-103E | Bourns Inc. |  | Active
33 | 1 | Q1 | Si2328DS | taylor_kicad:Q_NMOS_GSD | digikey-footprints:SOT-23-3 |  |  |  |  |  |  | DMN10H220L-7DICT-ND |  |  |  |  |  |  |  | DMN10H220L-7
34 | 6 | Q2, Q3, Q4, Q5, Q6, Q7 | 2N7002 | dk_Transistors-FETs-MOSFETs-Single:2N7002 | digikey-footprints:SOT-23-3 | https://www.onsemi.com/pub/Collateral/NDS7002A-D.PDF | Discrete Semiconductor Products | https://www.onsemi.com/pub/Collateral/NDS7002A-D.PDF | /product-detail/en/on-semiconductor/2N7002/2N7002NCT-ND/244664 | MOSFET N-CH 60V 115MA SOT-23 | 2N7002NCT-ND | MMBF0201NLT1GOSCT-ND |  | Transistors - FETs, MOSFETs - Single |  |  |  |  |  | 2N7002 | ON Semiconductor |  | Active
35 | 2 | R1, R2 | 2.2k 1% | Device:R | Resistor_SMD:R_0805_2012Metric | ~
36 | 1 | R3 | 24.1k/1% | Device:R | Resistor_SMD:R_0805_2012Metric | ~ |  |  |  |  |  | RMCF0805FT750RCT-ND
37 | 2 | R4, R5 | 5.1k | Device:R | Resistor_SMD:R_0805_2012Metric | ~ |  |  |  |  |  | RMCF0805FT130RCT-ND
38 | 1 | R6 | 249k | Device:R | Resistor_SMD:R_0805_2012Metric | ~ |  |  |  |  |  | RMCF0805FT750RCT-ND
39 | 2 | R7, R8 | 470R | Device:R | Resistor_SMD:R_0805_2012Metric | ~ |  |  |  |  |  | RMCF0805FT750RCT-ND
40 | 1 | R9 | 51k | Device:R | Resistor_SMD:R_0805_2012Metric | ~ |  |  |  |  |  | RMCF0805FT750RCT-ND
41 | 1 | R10 | 220R | Device:R | Resistor_SMD:R_0805_2012Metric | ~ |  |  |  |  |  | A129741CT-ND
42 | 2 | R11, R16 | 1k | Device:R | Resistor_SMD:R_0805_2012Metric | ~ |  |  |  |  |  | A106061CT-ND
43 | 6 | R12, R14, R15, R19, R23, R24 | 100R | Device:R | Resistor_SMD:R_0805_2012Metric | ~ |  |  |  |  |  | 311-100CRCT-ND
44 | 1 | R13 | 10k | Device:R | Resistor_SMD:R_0805_2012Metric | ~
45 | 2 | R17, R18 | 2.2K 1% | Device:R | Resistor_SMD:R_0805_2012Metric | https://fscdn.rohm.com/en/products/databook/datasheet/passive/resistor/chip_resistor/mcr-e.pdf |  |  |  |  |  |  |  |  | Farnell | 9239278 | RK73G1ETQTP2201D | KOA EUROPE GMBH | 120889581 |  |  | Resistor 2.2K M1005 1% 63mW
46 | 1 | R20 | DNP | Device:R | Resistor_SMD:R_0805_2012Metric | ~
47 | 1 | R21 | 10K | Device:R | Resistor_SMD:R_0805_2012Metric | ~ |  |  |  |  |  | 311-10.0KCRCT-ND
48 | 1 | R22 | 1K | Device:R | Resistor_SMD:R_0805_2012Metric | ~ |  |  |  |  |  | 311-10.0KCRCT-ND
49 | 1 | R25 | 3.9k | Device:R | Resistor_SMD:R_0805_2012Metric | ~ |  |  |  |  |  | 311-10.0KCRCT-ND
50 | 1 | S1 | RUN_SW | dk_Tactile-Switches:PTS645SM43SMTR92_LFS | digikey-footprints:Switch_Tactile_SMD_6x6mm_PTS645 | https://www.ckswitches.com/media/1471/pts645.pdf | Switches | https://www.ckswitches.com/media/1471/pts645.pdf | /product-detail/en/c-k/PTS645SM43SMTR92-LFS/CKN9112CT-ND/1146934 | SWITCH TACTILE SPST-NO 0.05A 12V |  | CKN9112CT-ND |  | Tactile Switches |  |  |  |  |  | PTS645SM43SMTR92 LFS | C&K |  | Active
51 | 4 | SW1, SW2, SW3, SW4 | SW_SPDT | Switch:SW_SPDT | digikey-footprints:Switch_Slide_11.6x4mm_EG1218 | ~ |  |  |  |  |  | 563-1151-ND
52 | 1 | TP1 | TestPoint | Connector:TestPoint | TestPoint:TestPoint_Keystone_5015_Micro-Minature | ~ |  |  |  |  |  | 36-5015CT-ND
53 | 2 | U3, U4 | AOZ8904CIL | 2021-10-21_05-38-11:AOZ8904CIL | footprints7:AOZ8904CIL |  |  |  |  |  |  | 785-1755-1-ND |  |  |  |  |  |  |  | AOZ8904CIL
54 | 1 | U5 | ISL54222AIUZ | 2021-10-22_05-57-19:ISL54222AIUZ | footprints10:ISL54222AIUZ |  |  |  |  |  |  | ISL54222AIUZ-ND |  |  |  |  |  |  |  | ISL54222AIUZ
55 | 1 | U6 | PDQ30-Q48-S5-D | acorn_motherboard-rescue:PDQ30-Q48-S5-D-PDQ30-Q48-S5-D | library:CONV_PDQ30-Q48-S5-D | 1 |  |  |  |  |  | 102-3897-ND |  |  | CUI Inc | Manufacturer Recommendations
56 | 1 | U7 | buffer | taylor_kicad:SN74LVC1G07QDCKTQ1 | footprints2:SN74LVC1G07QDCKTQ1 |  |  |  |  |  |  | TC7SZ07FULJ(CTCT-ND |  |  |  |  |  |  |  | TC7SH34FULJ(CTCT-ND
57 | 1 | U8 | buffer | taylor_kicad:SN74LVC1G07QDCKTQ1 | taylor_footprints:SN74LVC1G07QDCKTQ1 |  |  |  |  |  |  | TC7SZ07FULJ(CTCT-ND |  |  |  |  |  |  |  | TC7SH34FULJ(CTCT-ND
58 | 1 | U9 | RT9742SNGV | CM4IO:RT9742SNGV | Package_TO_SOT_SMD:SOT-23 | https://www.richtek.com/assets/product_file/RT9742/DS9742-09.pdf |  |  |  |  |  |  |  |  | Farnell | 2575555 | RT9742SNGV | RichTek | USWI00155 |  |  | Power Switch/Driver 1:1 N-Channel 500mA SOT-23-3
59 | 1 | U10 | Compute_Module_4_Connectors | Raspberry_Pi_Compute_Module_4:Compute_Module_4_Connectors | RPi_Compute_Module_4:Raspberry-Pi-4-Compute-Module
60 | 1 | U11 | MCP23016T-I/SO | 2021-11-13_04-51-52:MCP23016T-I{slash}SO | footprints5:MCP23016T-I&slash_SO
61 | 1 | Z1 | 15v/200mW | dk_Diodes-Zener-Single:MMSZ5231B-7-F | taylor_footprints:SOD-123 | https://www.diodes.com/assets/Datasheets/ds18010.pdf | Discrete Semiconductor Products | https://www.diodes.com/assets/Datasheets/ds30410.pdf | https://www.digikey.com/en/products/detail/diodes-incorporated/DDZ9702-7/700124 | DIODE ZENER 15V 500MW SOD123 |  | DDZ9702DICT-ND |  | Diodes - Zener - Single |  |  |  |  |  | DDZ9702-7 | Diodes Incorporated |  | Active
62 | 1 | Z2 | 28v/500mW | dk_Diodes-Zener-Single:MMSZ5231B-7-F | taylor_footprints:SOD-123 | https://www.diodes.com/assets/Datasheets/ds18010.pdf | Discrete Semiconductor Products | https://www.diodes.com/assets/Datasheets/ds18010.pdf | https://www.digikey.com/en/products/detail/diodes-incorporated/MMSZ5255B-7-F/814442 | DIODE ZENER 28V 500MW SOD123 |  | MMSZ5255B-FDICT-ND |  | Diodes - Zener - Single |  |  |  |  |  | MMSZ5255B-7-F | Diodes Incorporated |  | Active

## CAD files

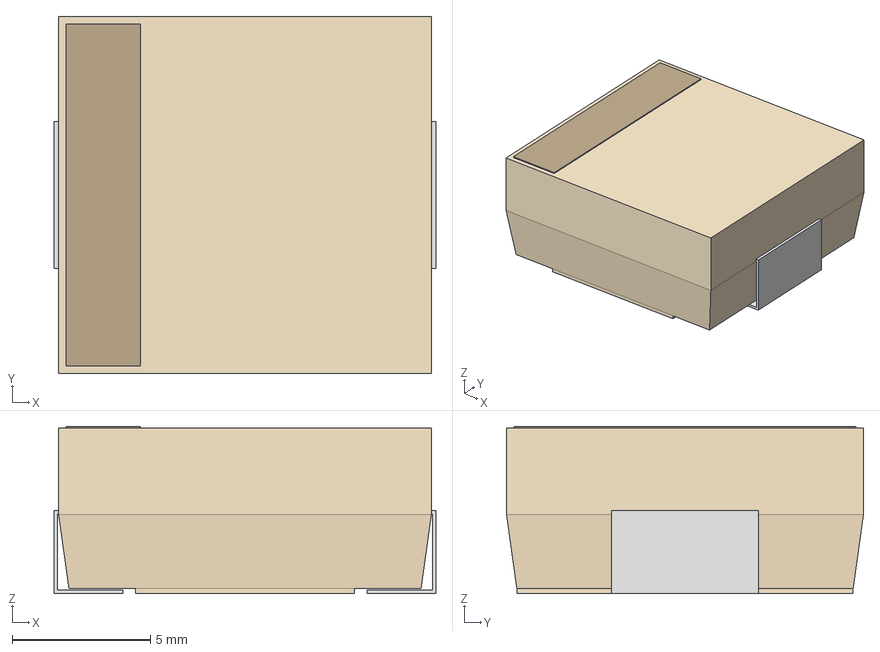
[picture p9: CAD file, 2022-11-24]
cm4_robot_board/parts/2022-11-05_07-16-47/STEP/IND_MWSA1206S_SNL.step
13.8 x 12.9 x 6.04 mm

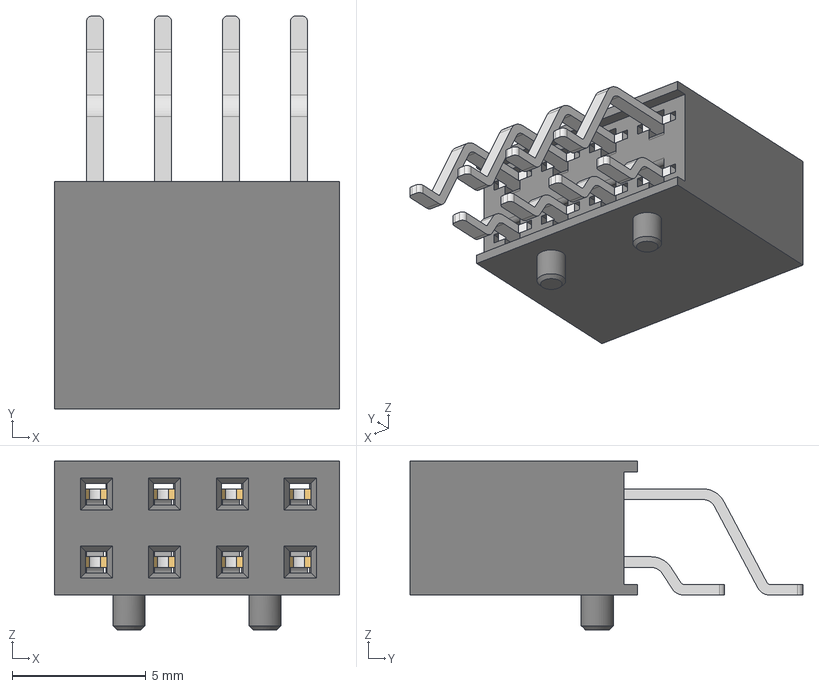
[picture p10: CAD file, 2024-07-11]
cm4_robot_board/parts/Download_STP_610108249221_rev1.stp
10.7 x 14.7 x 6.30 mm
6103xx249221_PIN COURTE x 4
6103xx249221_PIN LONGUE x 4

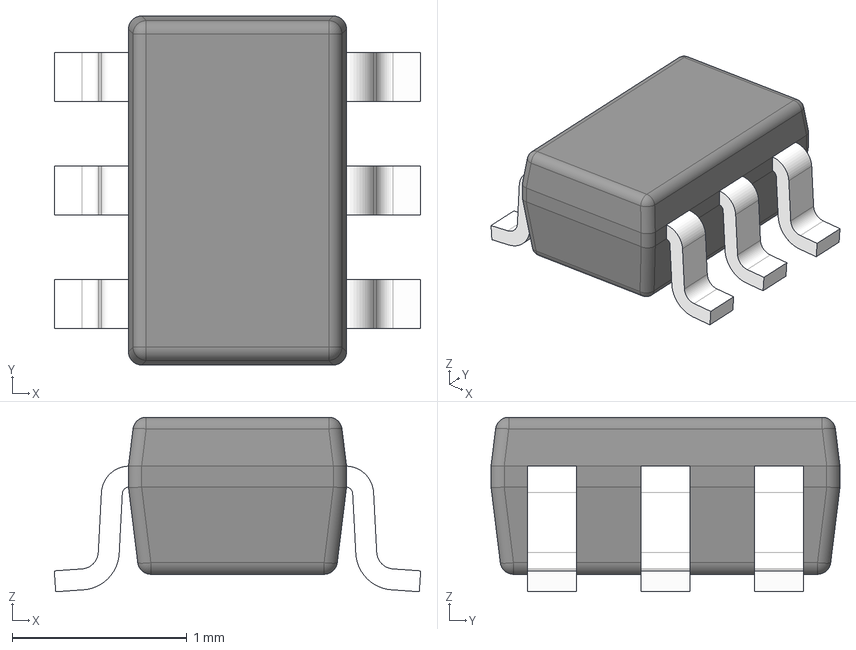
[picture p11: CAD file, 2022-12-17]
cm4_robot_board/parts/STEP/DCK0006A.stp
2.10 x 2.00 x 1.00 mm
BODY-SOT
LEAD-SOT x 6
PIN1-ID

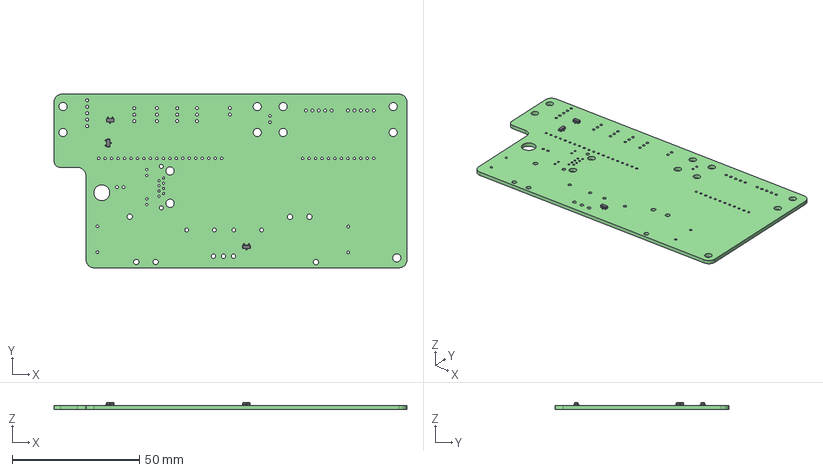
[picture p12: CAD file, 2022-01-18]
odrive_interface/acorn-odrive-interface.step
138.5 x 68.2 x 2.85 mm
acorn-odrive-interface PCB

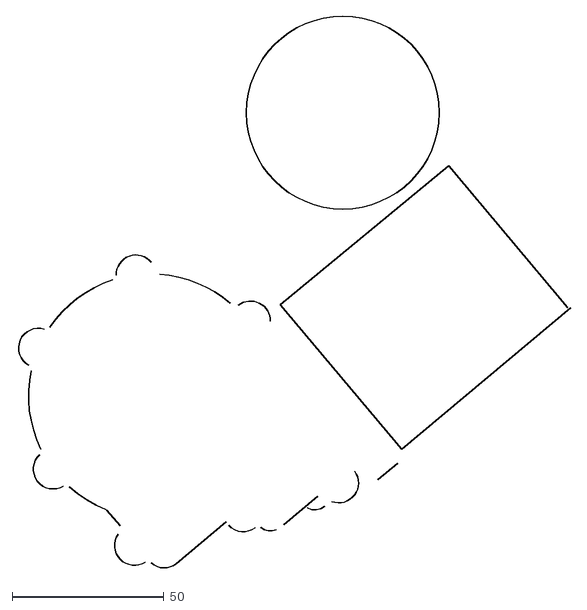
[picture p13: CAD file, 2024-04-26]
soft_start/fork.dxf
182.6 x 182.3

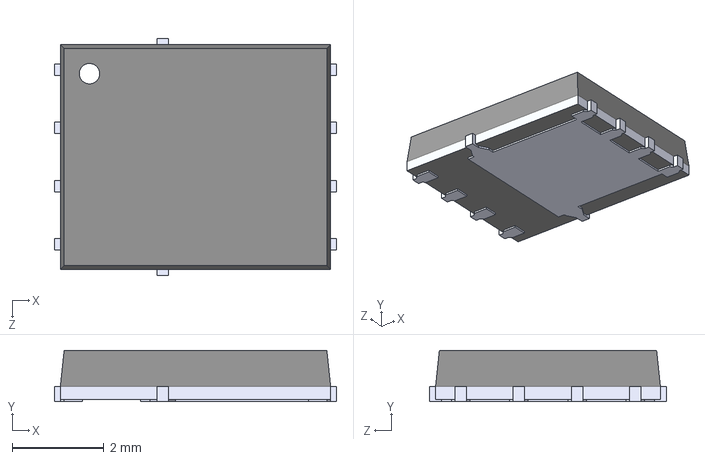
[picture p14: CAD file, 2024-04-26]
soft_start/parts/PowerPAK-SO8.STEP
6.15 x 1.12 x 5.16 mm

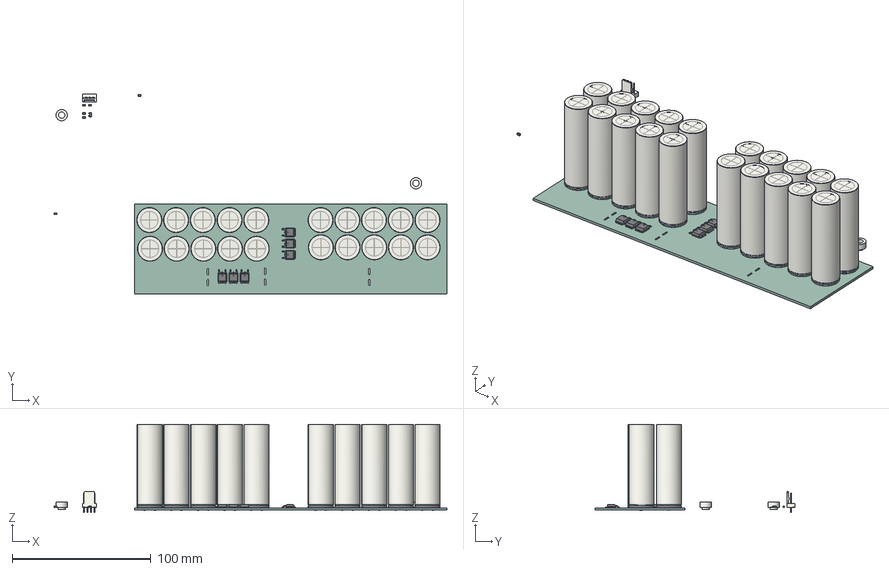
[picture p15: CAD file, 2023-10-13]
supercap/supercap/supercap2.step
282.9 x 144.3 x 63.6 mm
supercap PCB

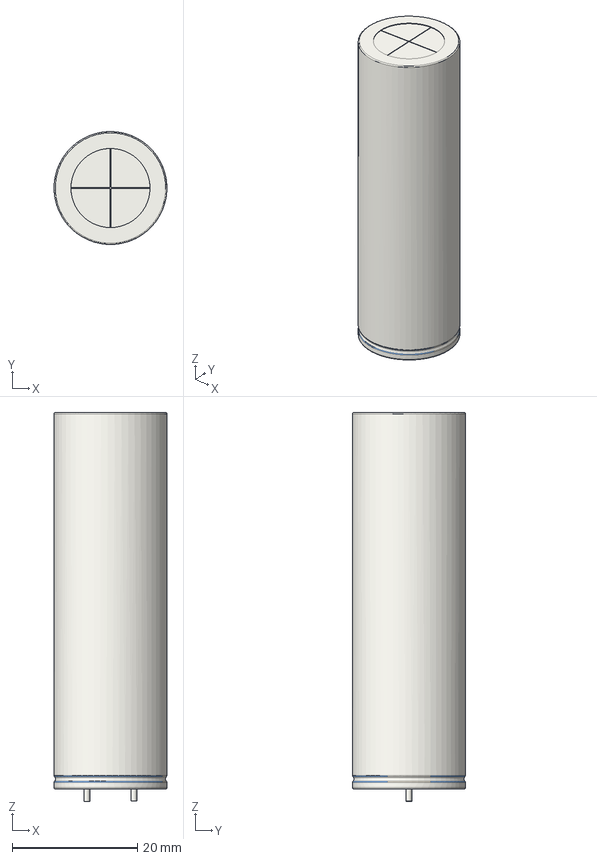
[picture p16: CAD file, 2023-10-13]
supercap/supercap_simple/CP_Radial_D18.0mm_P7.50mm_L60.0mm.step
18.0 x 18.0 x 62.0 mm

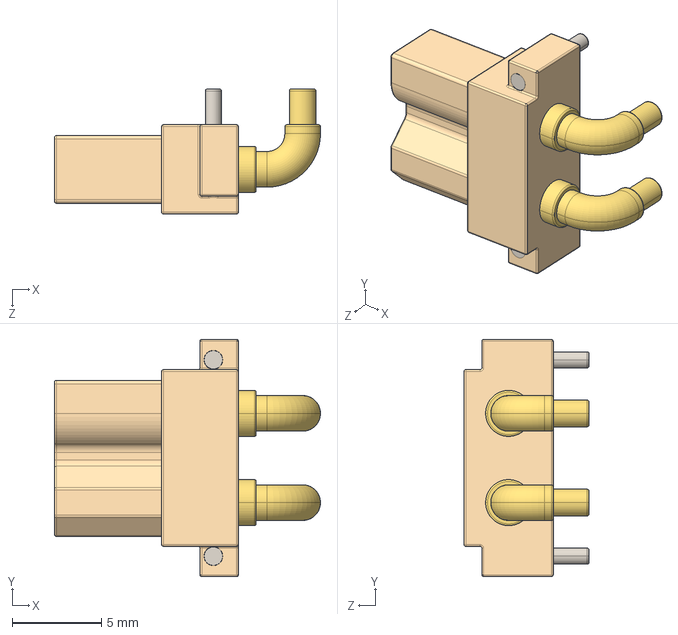
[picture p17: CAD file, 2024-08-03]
supercap/supercap_simple/parts/XT30PW-F.STEP
14.9 x 13.3 x 7.00 mm

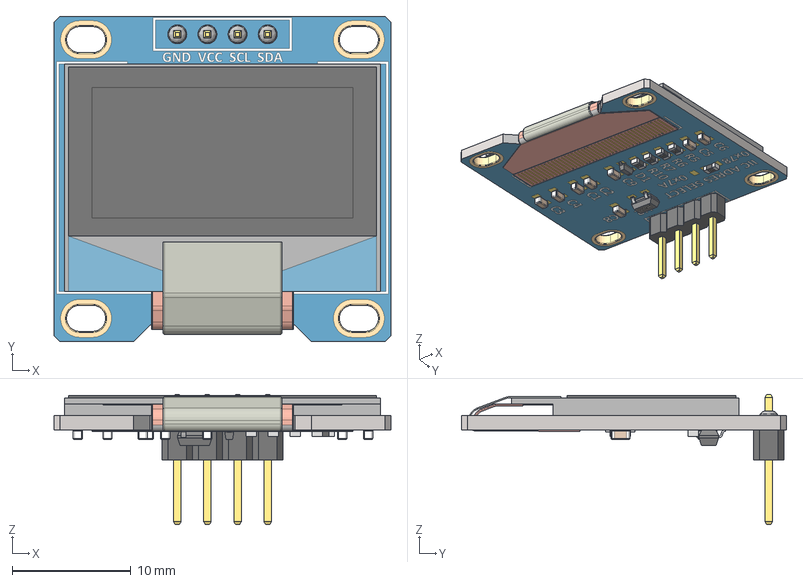
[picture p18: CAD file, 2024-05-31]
cm4_robot_board/parts/Pantalla OLED 0.96'' 128x64.stp
28.4 x 27.4 x 11.0 mm
SOT-23_TOR
RES_CR16_MTK_1 x 4
RES_CR16_MTK
SOD323F_DIO

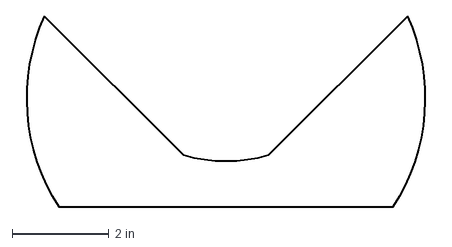
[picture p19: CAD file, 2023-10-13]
soft_start/capacitors.dxf
8.65 x 3.94 in

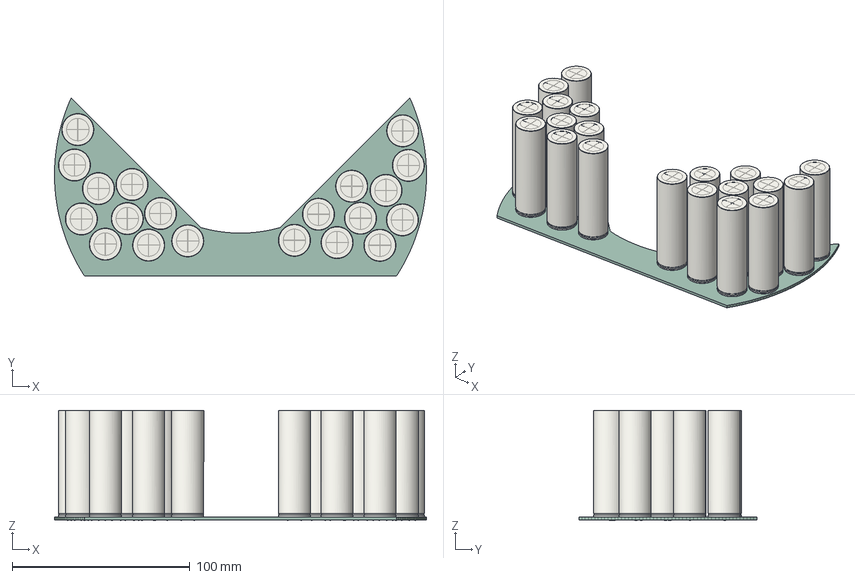
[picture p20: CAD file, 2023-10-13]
supercap/supercap/supercap.step
209.0 x 100.0 x 62.0 mm
_autosave-supercap PCB

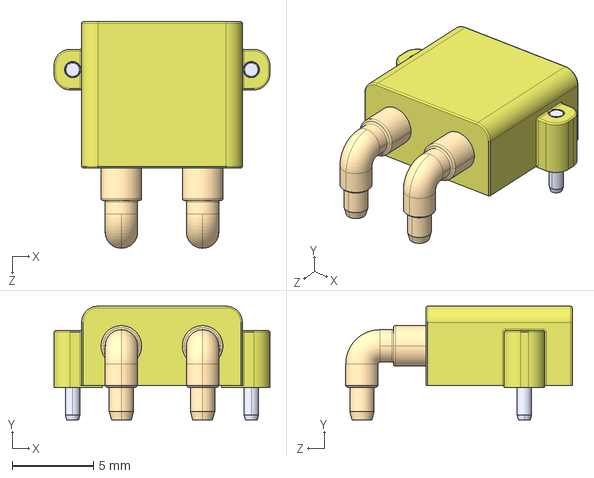
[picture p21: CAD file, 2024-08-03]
supercap/supercap_simple/parts/XT30PW-M--3DModel-STEP-269445.STEP
13.3 x 7.00 x 14.0 mm

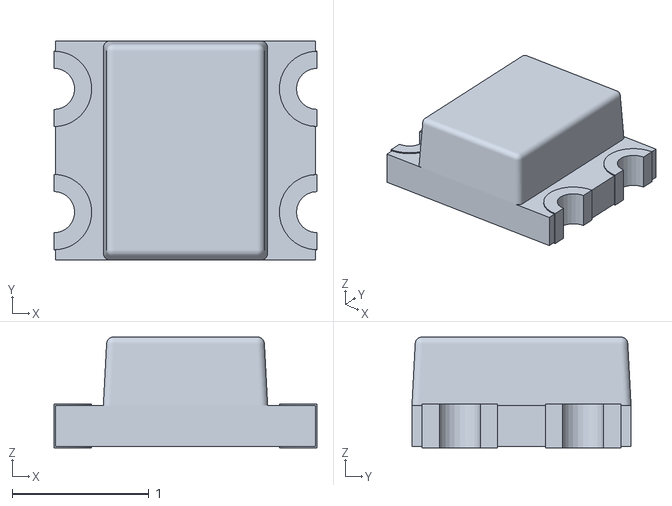
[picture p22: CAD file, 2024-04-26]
cm4_robot_board/parts/LED-ARRAY-SMD_4P-L1.9-W1.6-BL-CW.obj
1.92 x 1.60 x 0.81

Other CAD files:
supercap/supercap/supercap3.step
supercap/supercap_simple/parts/Anderson P45_dual.step
cm4_robot_board/parts/CONN-TH_5P-P2.54_HCTL_HC-2510-5AW.obj
cm4_robot_board/parts/SW-TH_SS12D07VG4.obj
cm4_robot_board/parts/5556416-1.stp
cm4_robot_board/parts/DWV0008A.stp
cm4_robot_board/parts/HR911105A.step
cm4_robot_board/parts/LED-ARRAY-SMD_4P-L2.1-W2.1-TL_NH-B2020RGBA.obj
cm4_robot_board/parts/LED-SMD_4P-L2.0-W1.3-RD-TL.obj
cm4_robot_board/parts/M-RJE08-188-0X10-REVG1.IGS
cm4_robot_board/parts/M-RJE08-188-0X10-REVT1.STEP
cm4_robot_board/parts/MS12ANW03.stp
cm4_robot_board/parts/MSAS-08PFFR-SF7003-STP.STP
cm4_robot_board/parts/SS-650810-A-NF.stp
cm4_robot_board/parts/USB4105-GF-A--3DModel-STEP-56544.STEP
cm4_robot_board/parts/c-1-1747981-2-l-3d.stp
cm4_robot_board/parts/c-1747981-2-l-3d.stp
cm4_robot_board/parts/c-8-1747981-1-l-3d.stp
cm4_robot_board/parts/sdr0403.stp
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

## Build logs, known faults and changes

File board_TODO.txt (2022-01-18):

motherboard:
	fix size of C5, 8mm diameter too small
	USB diode doesn't work, I guess need ideal diode to handle more power? LTC4412 controller and p-ch mosfet. need reverse current protection mostly
	https://www.ti.com/lit/an/slvae57b/slvae57b.pdf?ts=1641991127253
	fork board, flip camera connectors. delete camera connectors from main board
	add camera LED control
	add something to the design to hold CM4 in reset until power is stabilized? why does it not always boot at power on?
	are any switches backwards?
	add ground test points
	check the size of the PTH holes used on the DC DC converter
	consider a power on delay chip attached to GLOBAL_EN, or debug inconsistent power on condition. or is that due to incorrectly seated CM4?
	
odrive aux board:
	footprint for buffers is wrong, copy from motherboard

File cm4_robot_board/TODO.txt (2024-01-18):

RTC
https://jlcpcb.com/partdetail/NxpSemicon-PCF85063ATAAZ/C2157792
https://forums.raspberrypi.com/viewtopic.php?f=98&t=293632

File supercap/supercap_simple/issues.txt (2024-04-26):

input mosfet arrangement incorrect - see https://www.ti.com/lit/an/slva948/slva948.pdf
current sensing should not be unidirectional for input power at least. and care must be taken
to ensure that output current sensing is the correct direction (seems ok)

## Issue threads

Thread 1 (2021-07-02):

Can you list places to purchase or have made?

ebo, 2021-07-02:
I am interested in getting involved, but I need to first access the time I can commit to the project (I am already overbooked).  That said, besides working as a software engineer contractor at NASA/NOAA, I also served two formal apprenticeships in my 20's with a tool and die machinist, and a master blacksmith.  I should be able to help design, prototype, and test tooling.  In addition, I have an electronic technicians diploma, but that only makes me relatively safe to work with the electronics, not help much with the design.

BTW, some of my past work at NASA involved processing 100's of terabytes of sub-meter satellite imagery to identify trees and shrubs in the Sahel, and I still work with, and teach, python on the supercomputers.

Anyway, getting back to my question -- can you list locations to get various parts, including the RPi hat?  I quickly skimmed the site and could not find the info.

I look forward to learning more about the site, and see if I can do stuff to help.

tlalexander, 2022-01-18:
Hello! Sorry for the delay. I just finished a complete redesign of the hardware, now based on the Raspberry Pi Compute Module (CM4). There are no sources to order the boards yet, but we will be working towards a production release and wherever we get things fabbed, we will share as much as possible on how to get them made. In time once the project begins to get some traction, hopefully multiple sources of compatible boards will pop up. But that is some time away.

tlalexander, 2022-01-18:
Currently I order PCBs and stencils from JLCPCB and hand assemble them at home. But we will move towards an outside assembler in the future and I will see about a group buy on the forum once I get all of that fab process working.

OpenSourceIronman, 2022-12-10:
I would also love to purchase 3 to 5 raw PCBs to help offset your initial costs.

tlalexander, 2022-12-30:
Thank you! We now order fully assembled PCBs from JLCPCB. I just got back the new PCBs and we are honing in on a stable design. Once we get to that point I will work on improving our documentation and cleaning up our resources, in anticipation of full kit sales.

@OpenSourceIronman Would you prefer to buy some PCBs over making a donation? I have thought about selling merchandise to people who like a little stuff for their donation. I am curious what motivates you. I wanted to print and sell some high quality posters of the robot, but PCBs is an interesting idea too. One note is that shipping stuff takes time so it can end up costing us a fair bit of money to do it! But I want to at least hear what people are interested in.

OpenSourceIronman, 2022-12-30:
I like collecting cool hardware so yes I would be willing to pay 150% above your cost for prototype hardware instead of donation.

Ship it nice and slow to save cost. I can send my address via Twitter @BlazeDSanders or Mastodon @blazesanders@tech hub.social

ebo, 2022-12-31:
It has been long enough since I first came across the project.  I have a couple of use cases for setting up a low mobile platform with fork-lift tines to move small pallets into a crawl space for storage.  Other projects include precision seeders, transplanters, and possibly inspection.  I can see doing some image processing and building a weeder as well.  I would need to check to see, but the weeders I would probably base mine off of may still be under a patent lock (not like I am planing to sell the beasts, but due diligence is what it is).  Anyway, once I have a platform that I know and learn to trust, it is hard to say what all I would do with it -- I picked up a couple of small 20hp tractors with blown engines, but the hydraulic motors on the wheels still looked good, so I could step the power up[ to 10 to 30HP, and put it on a converted machine.  Anyway, not bad for literally $10 at auction, and the one has 5x hydraulic motors and the pump...

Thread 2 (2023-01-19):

Additional connectors for peripherals

samuk, 2023-01-19:
I was wondering if, on the next iteration of the board, you could squeeze in three additional connectors

1) UEXT - Underrated IMHO https://www.olimex.com/Products/Modules/ Olimex produce some nice open hardware bits, notably LoRa modules with UEXT

2) MikroBUS [shuttle 2 x 8 ](https://www.mikroe.com/mikrobus-shuttle-127mm-2x8-pin-box-header-smd-male) header, this connects to [daughter board](https://www.mikroe.com/mikrobus-shuttle) and [1407 sensors/ peripherals](https://www.mikroe.com/click)

3) Qwiic because it's small, and why not..

tlalexander, 2023-01-20:
Seems like good suggestions, thanks!

samuk, 2023-01-22:
If you were up for adding some extra connectors I wonder if it would be worth moving to the Nano ITX form factor? You could squeeze in a Pi header then. I realise you probably won't need it for an acorn use case, but it might make the board more appealing for a general robotics audience.
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

tlalexander, 2023-01-22:
I tend to want as few constraints as possible unless there is a specific motivation. What would be the benefit of doing so?

samuk, 2023-01-23:
The benefit for me is that I can design a robot base for the Nano Atx standoffs and use either the Beaglebone AI-64 or this board.  I dunno if there's any benefit for you aside from perhaps a few more users. Same for Pi header too I suppose.

samuk, 2024-01-12:
Bumping the Qwiic and Microbus header suggestion as it looks like your working on a new iteration

MikroBUS [shuttle 2 x 8 ](https://www.mikroe.com/mikrobus-shuttle-127mm-2x8-pin-box-header-smd-male)header, this connects to [daughter board](https://www.mikroe.com/mikrobus-shuttle) and [1407 sensors/ peripherals](https://www.mikroe.com/click)

Qwiic because it's small, and why not..

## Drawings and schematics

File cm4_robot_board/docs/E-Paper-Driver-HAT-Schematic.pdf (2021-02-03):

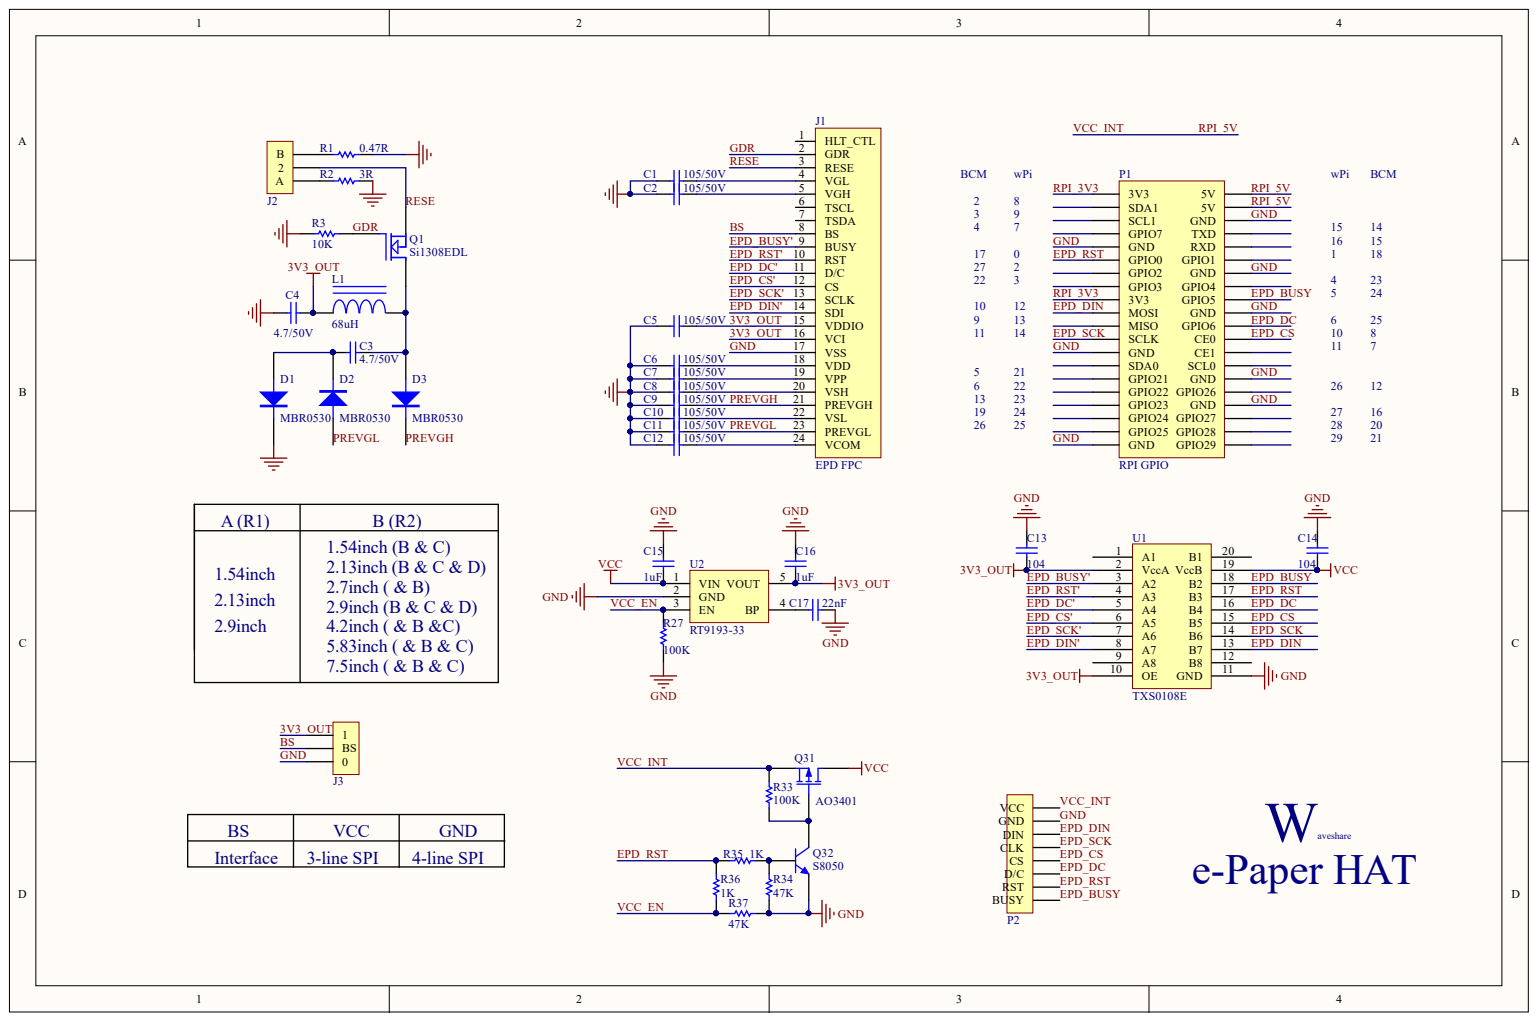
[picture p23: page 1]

C7 | | 1 0 5 / 5 0 V 1 9
C8 | | 1 0 5 / 5 0 V 2 0
C9 | | 1 0 5 / 5 0 V PRE V G H 2 1
C1 0 | | 1 0 5 / 5 0 V 2

C1 1 | | 1 0 5 / 5 0 V PRE V G L 2 3
C1 2 | | 1 0 5 / 5 0 V 2

BS | VCC | GN D
Interface | 3-line SPI | 4-line SPI

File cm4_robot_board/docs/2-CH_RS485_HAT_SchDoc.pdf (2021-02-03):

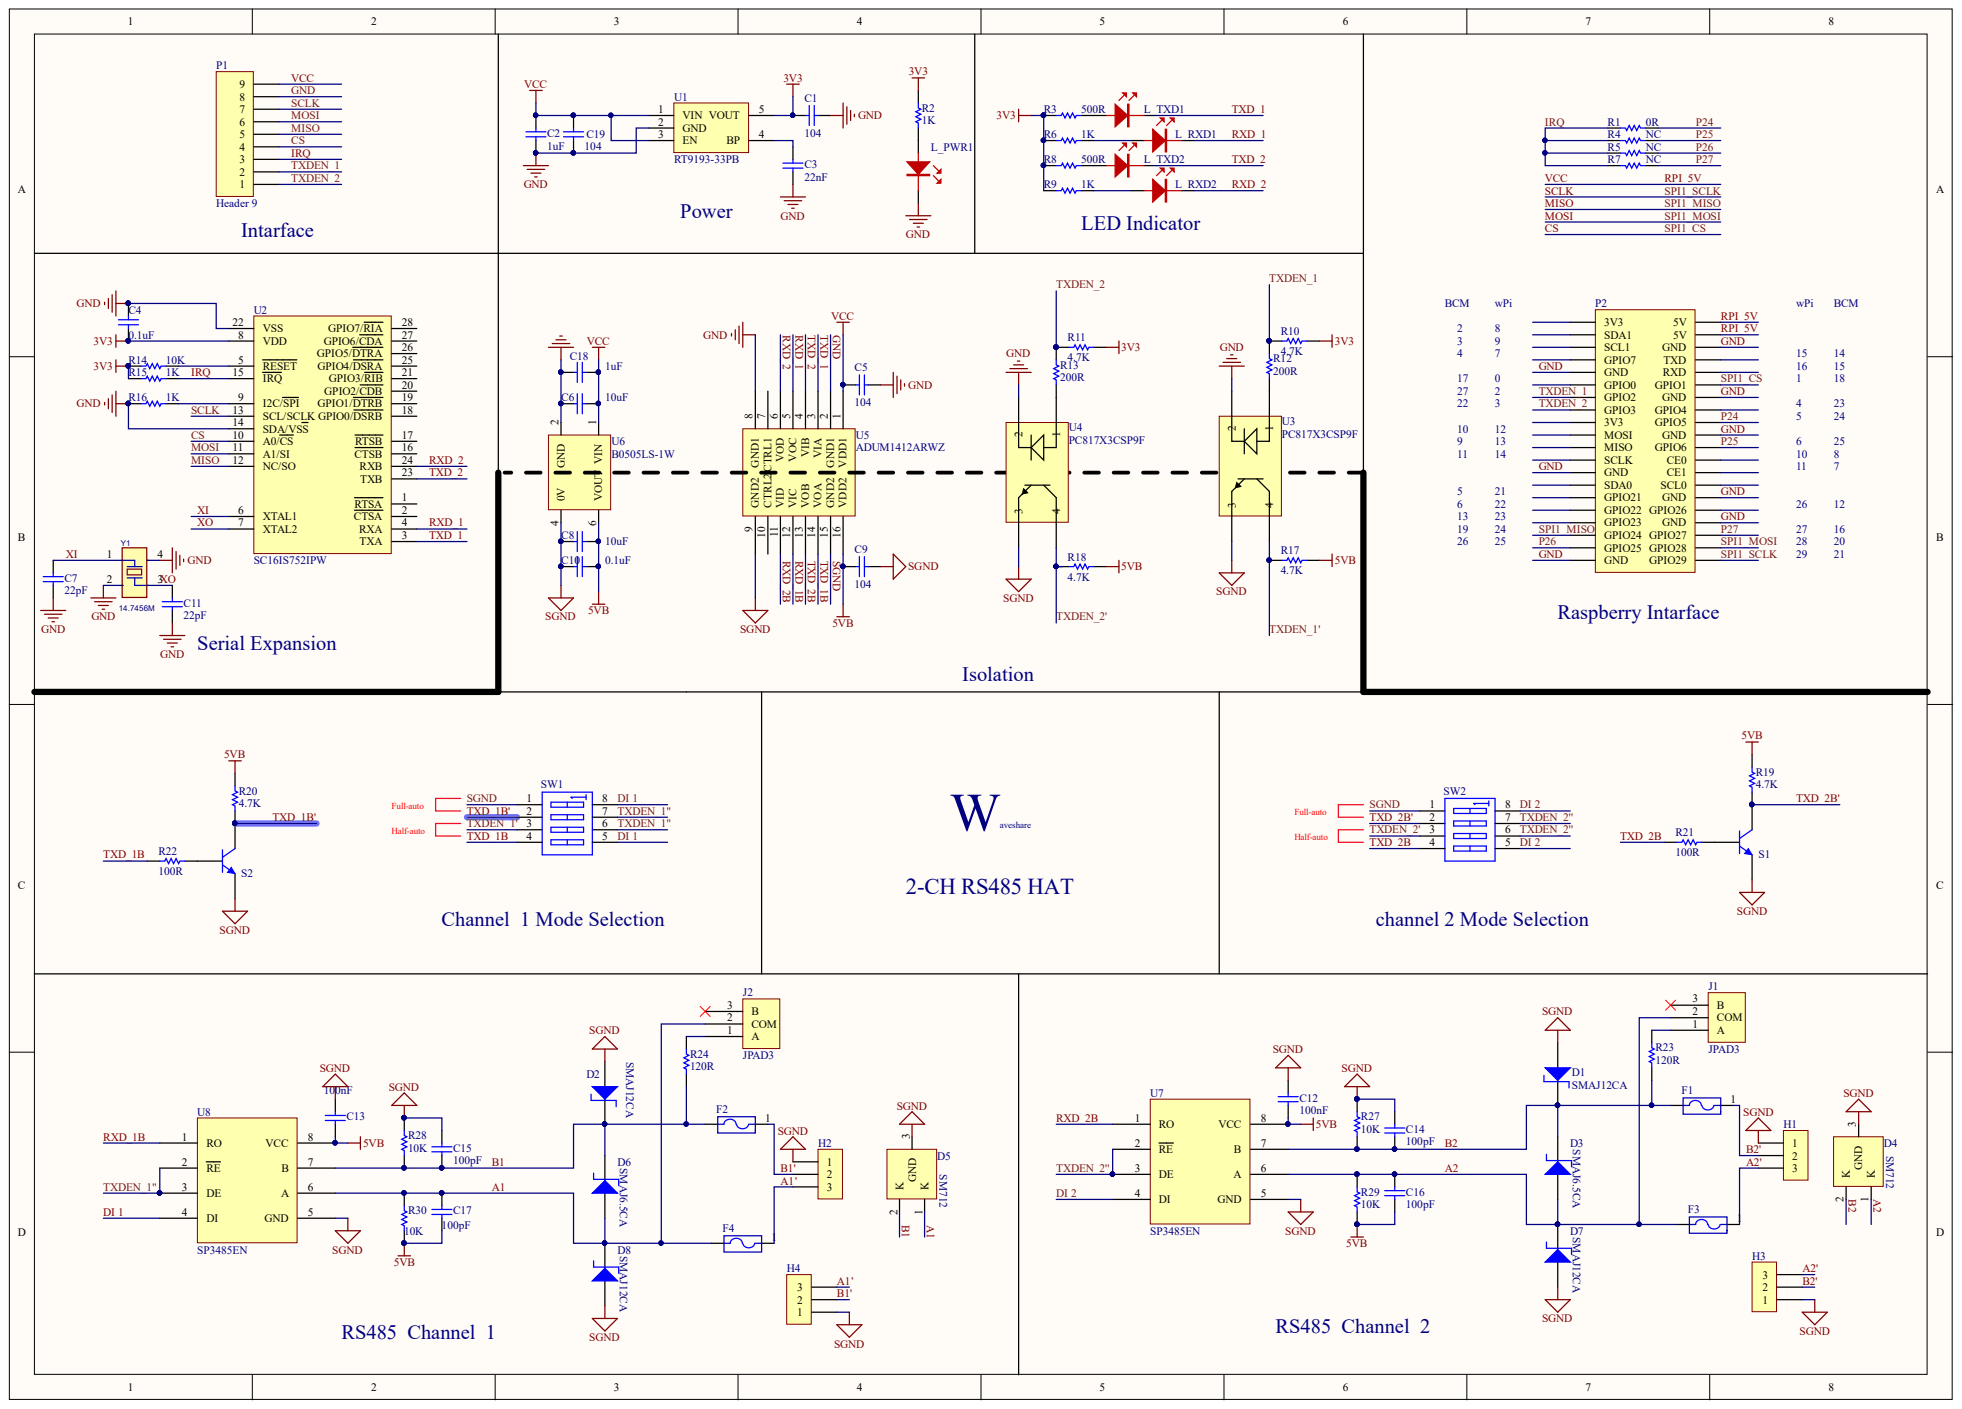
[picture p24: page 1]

VDD1 1 GND1 2 VIA 3 VIB 4 VOC 5 VOD 6 CTRL1 7 GND1 8 GND2 9

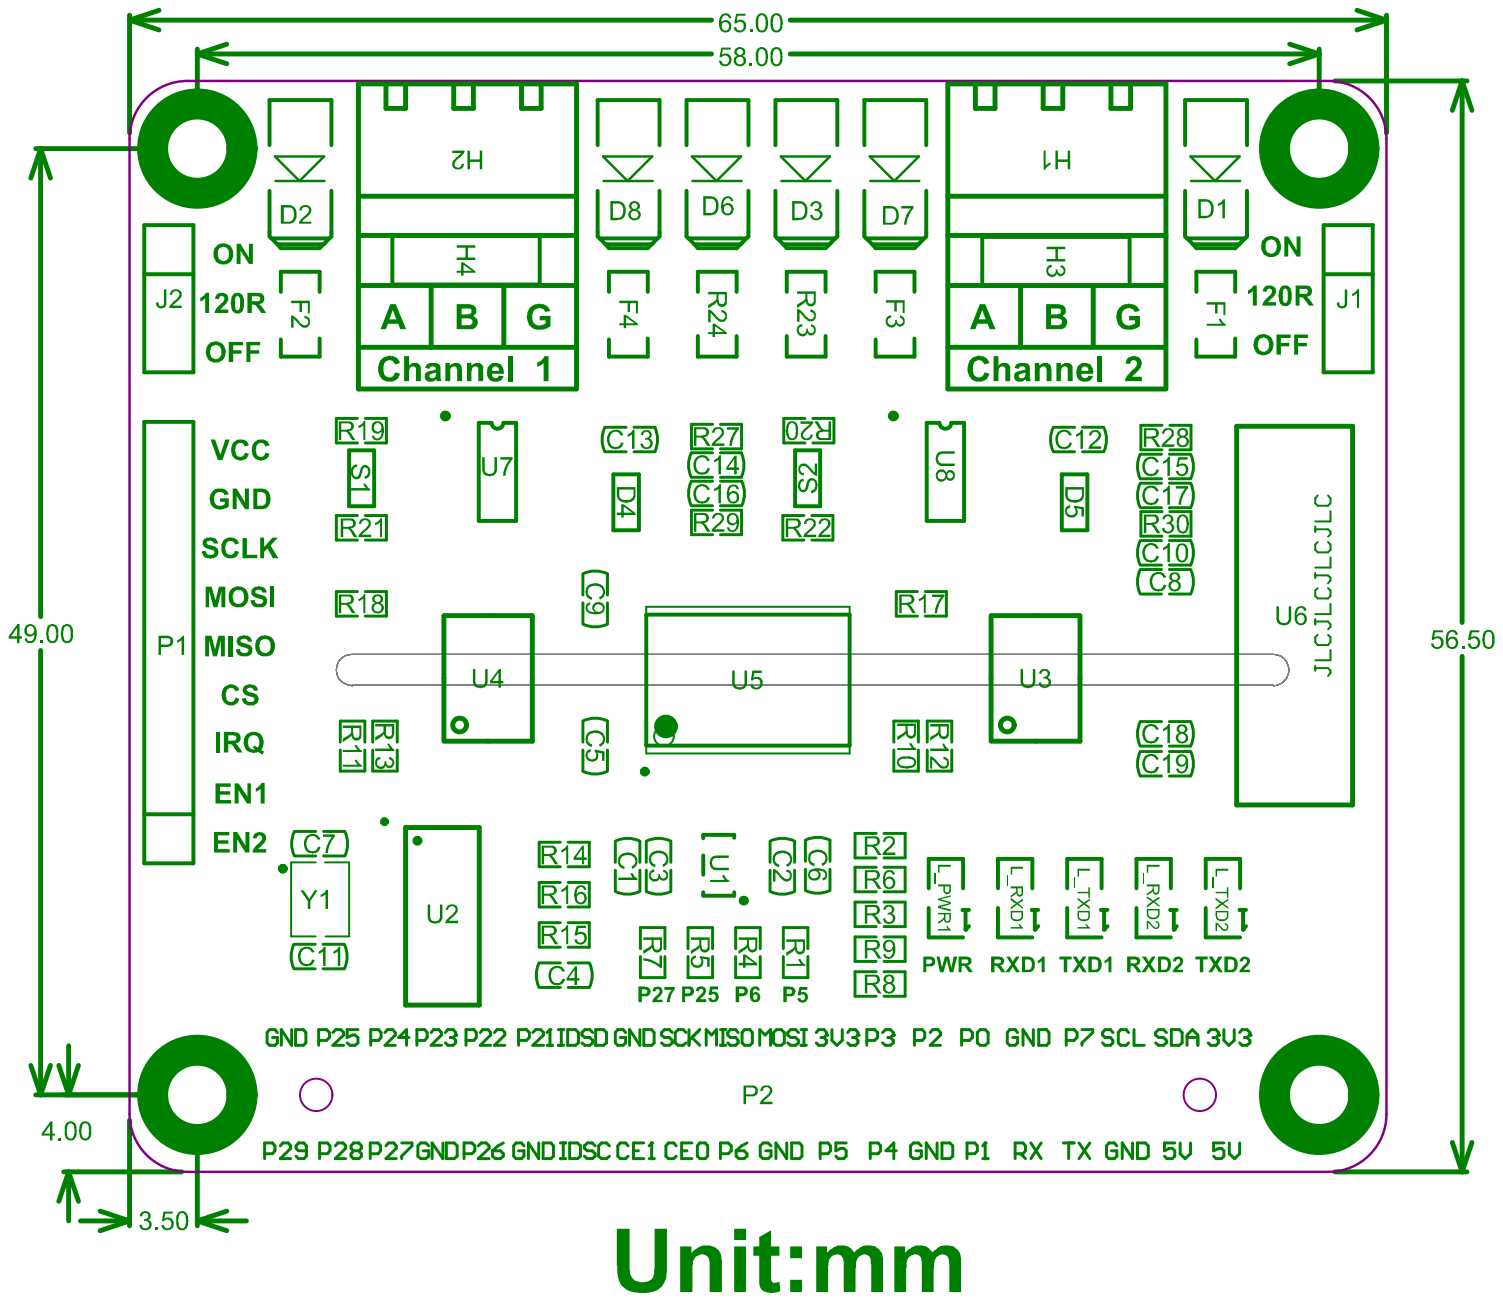
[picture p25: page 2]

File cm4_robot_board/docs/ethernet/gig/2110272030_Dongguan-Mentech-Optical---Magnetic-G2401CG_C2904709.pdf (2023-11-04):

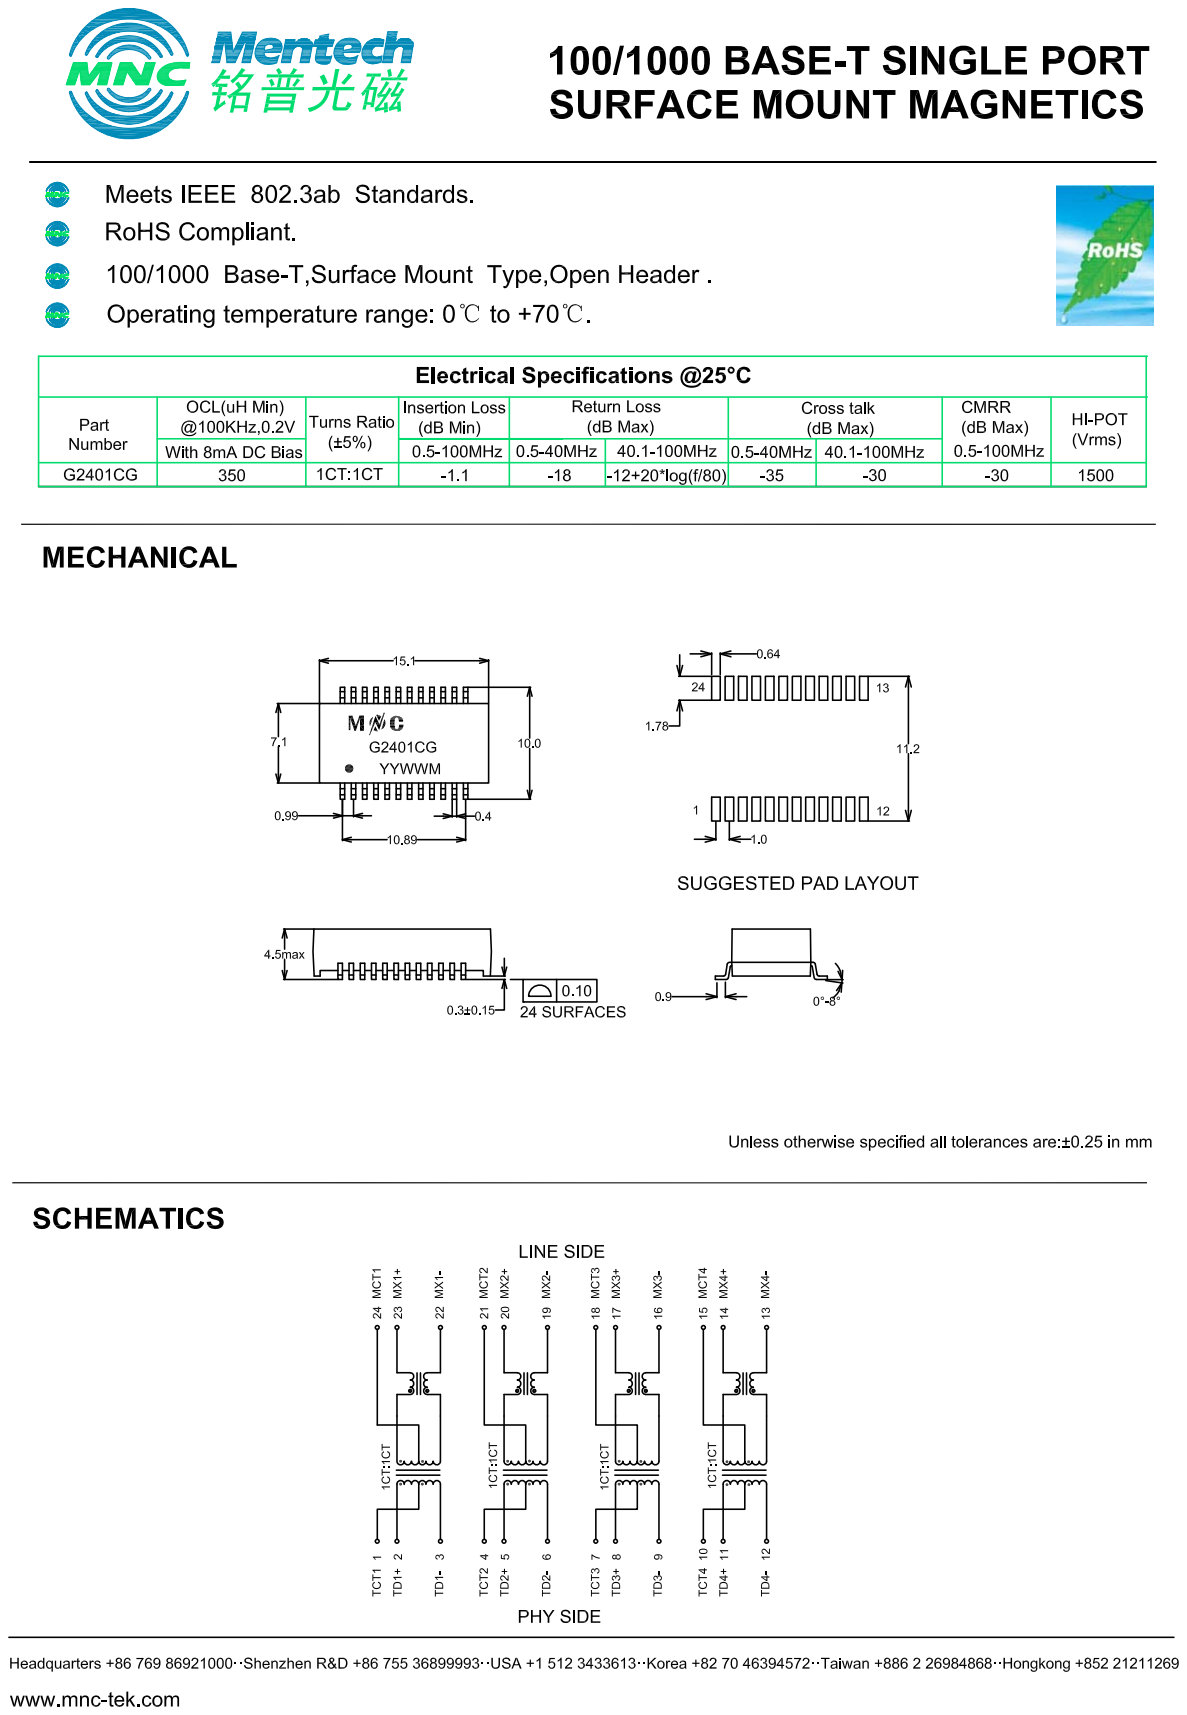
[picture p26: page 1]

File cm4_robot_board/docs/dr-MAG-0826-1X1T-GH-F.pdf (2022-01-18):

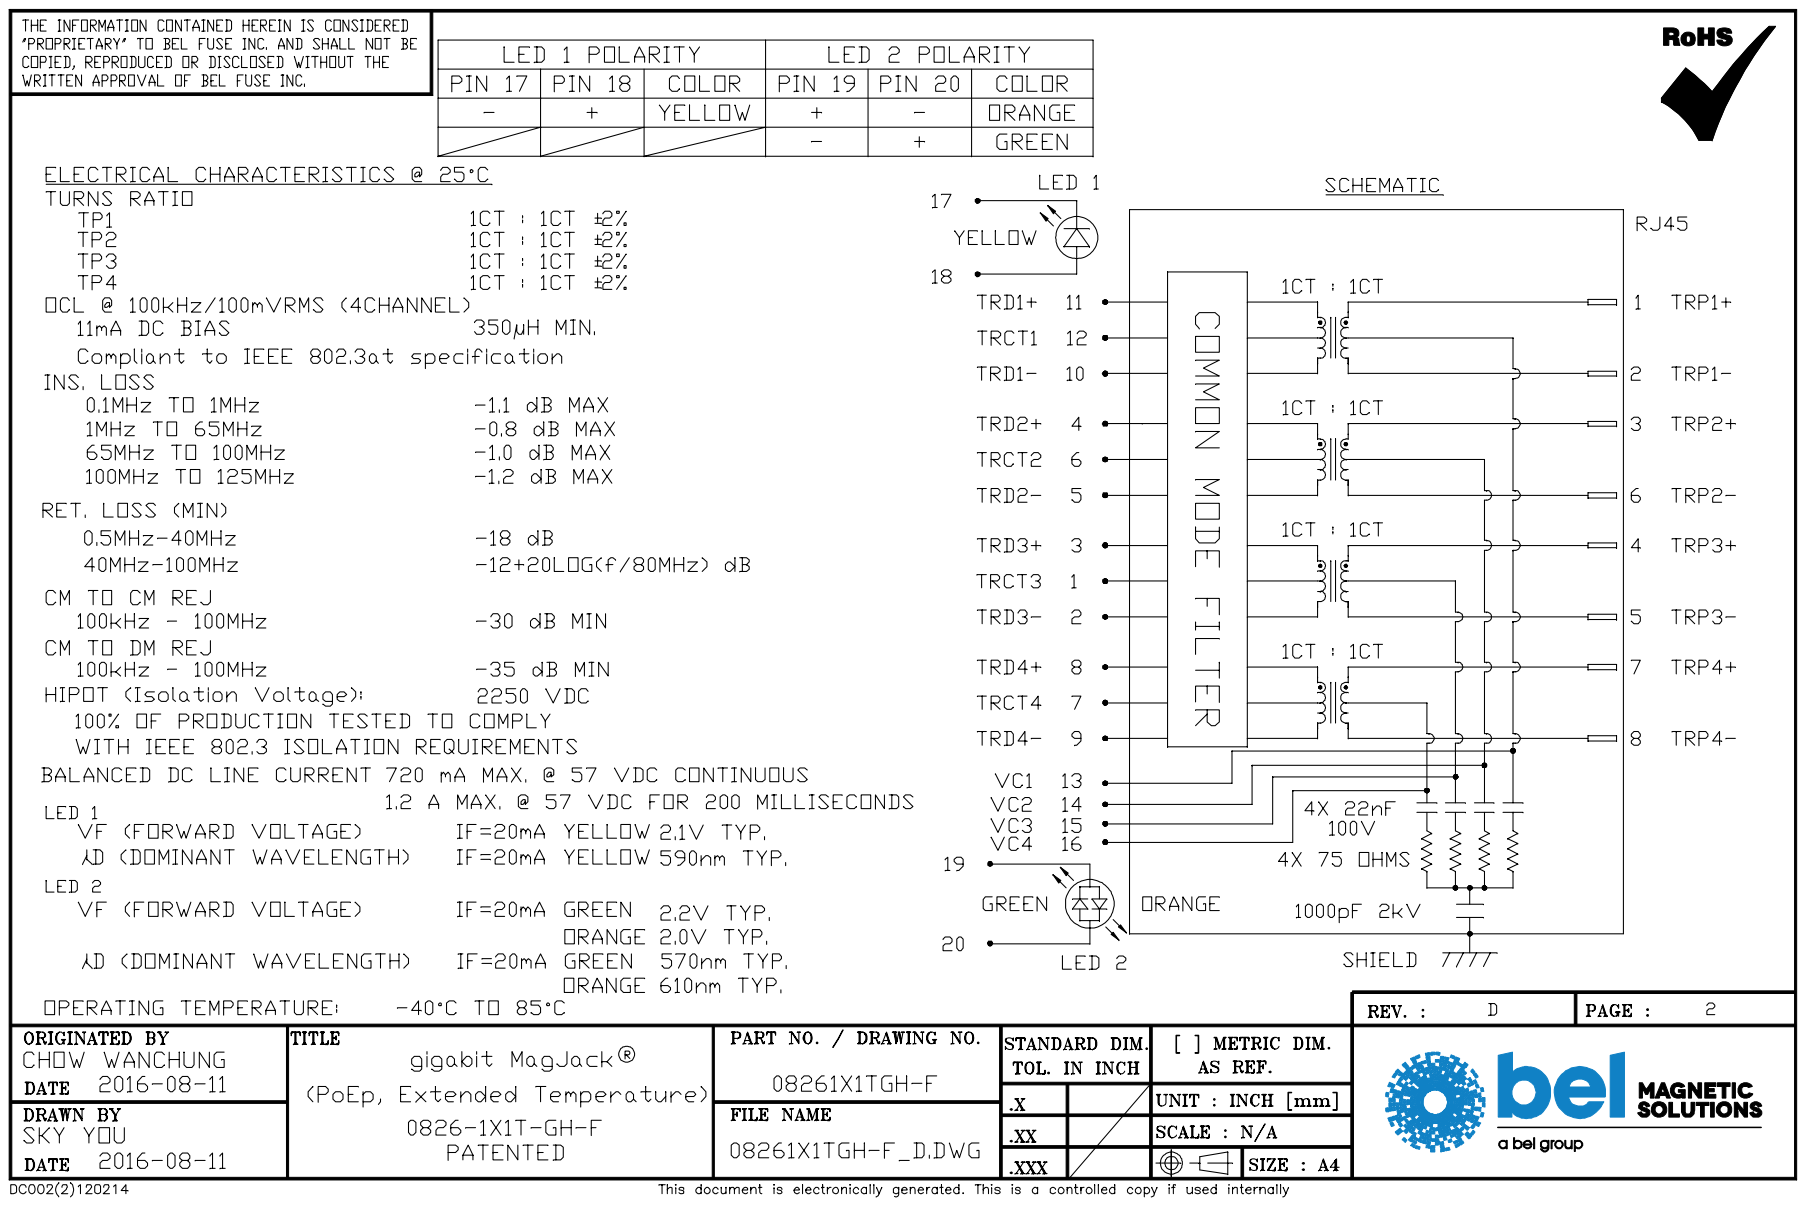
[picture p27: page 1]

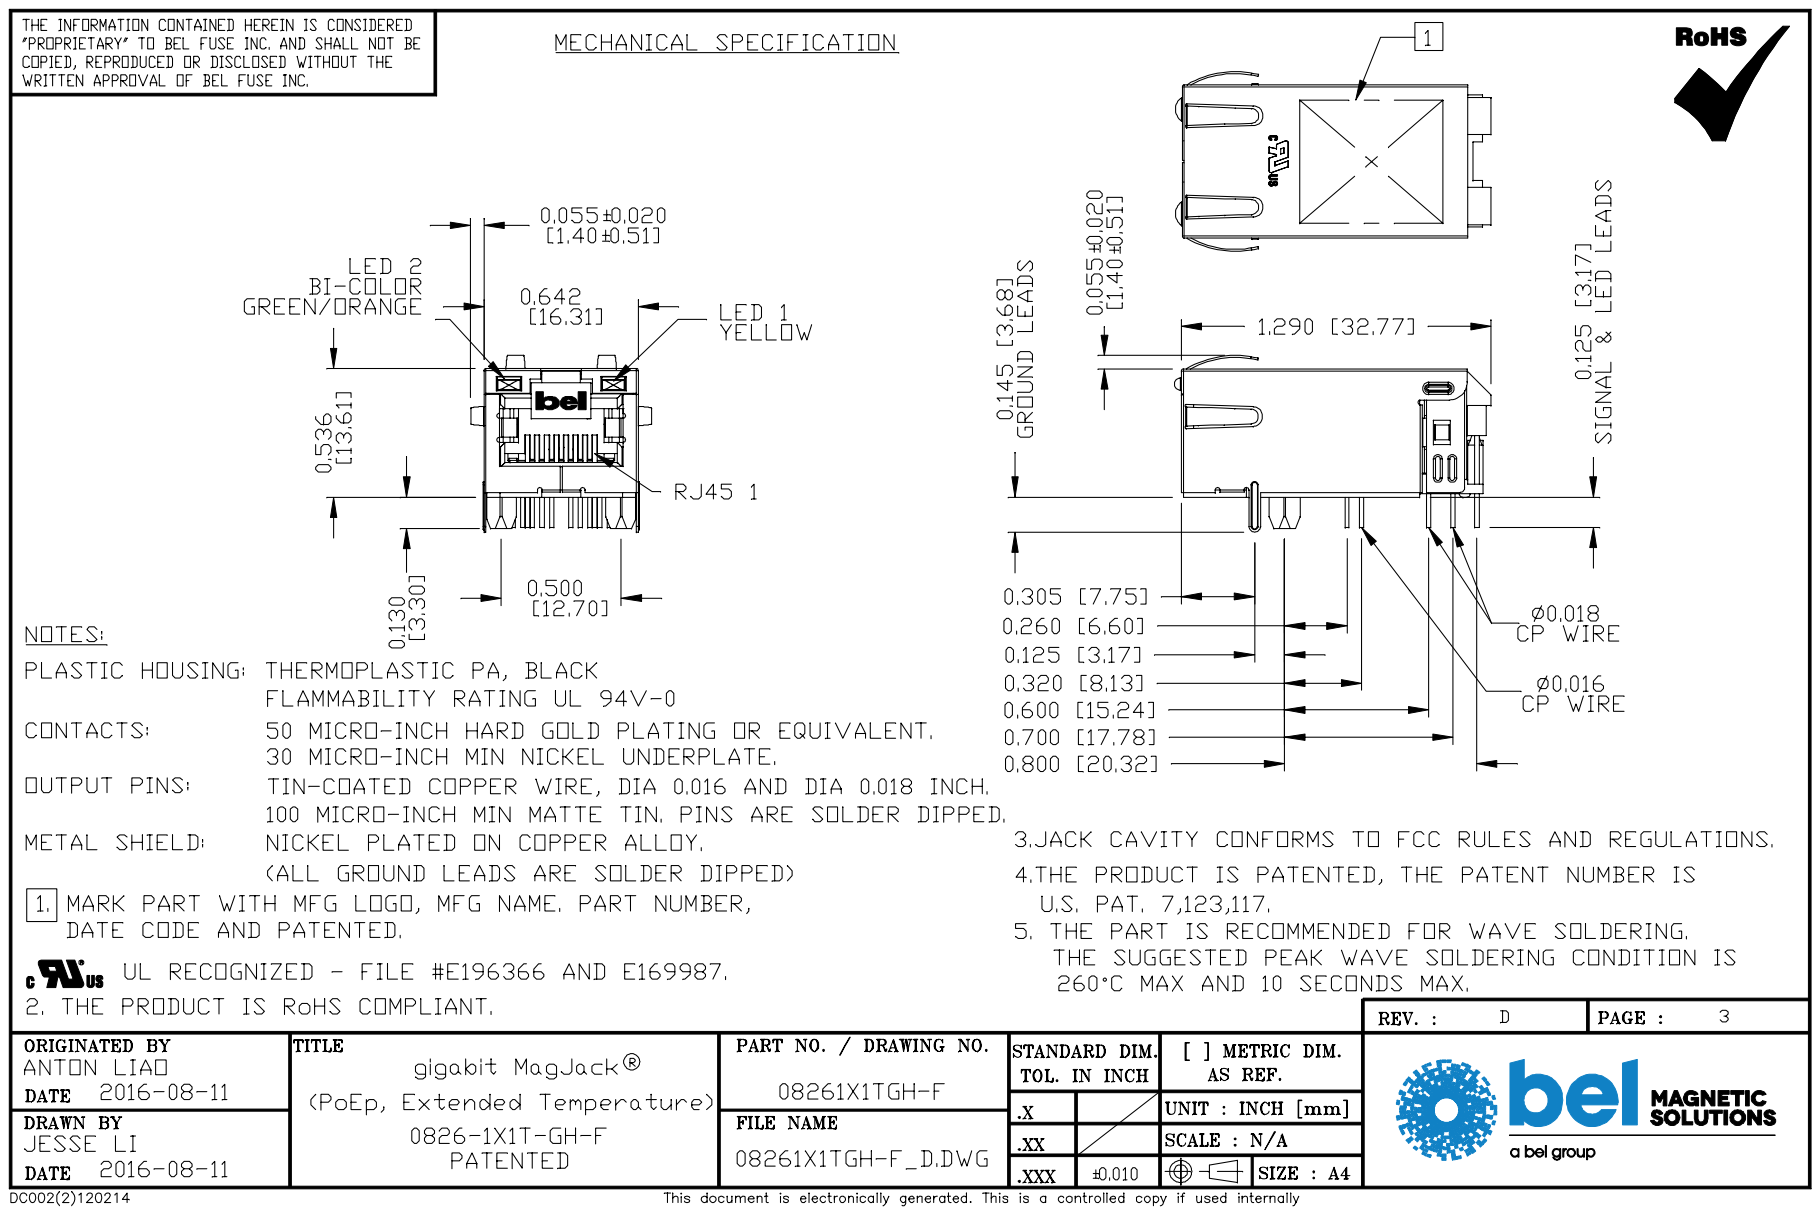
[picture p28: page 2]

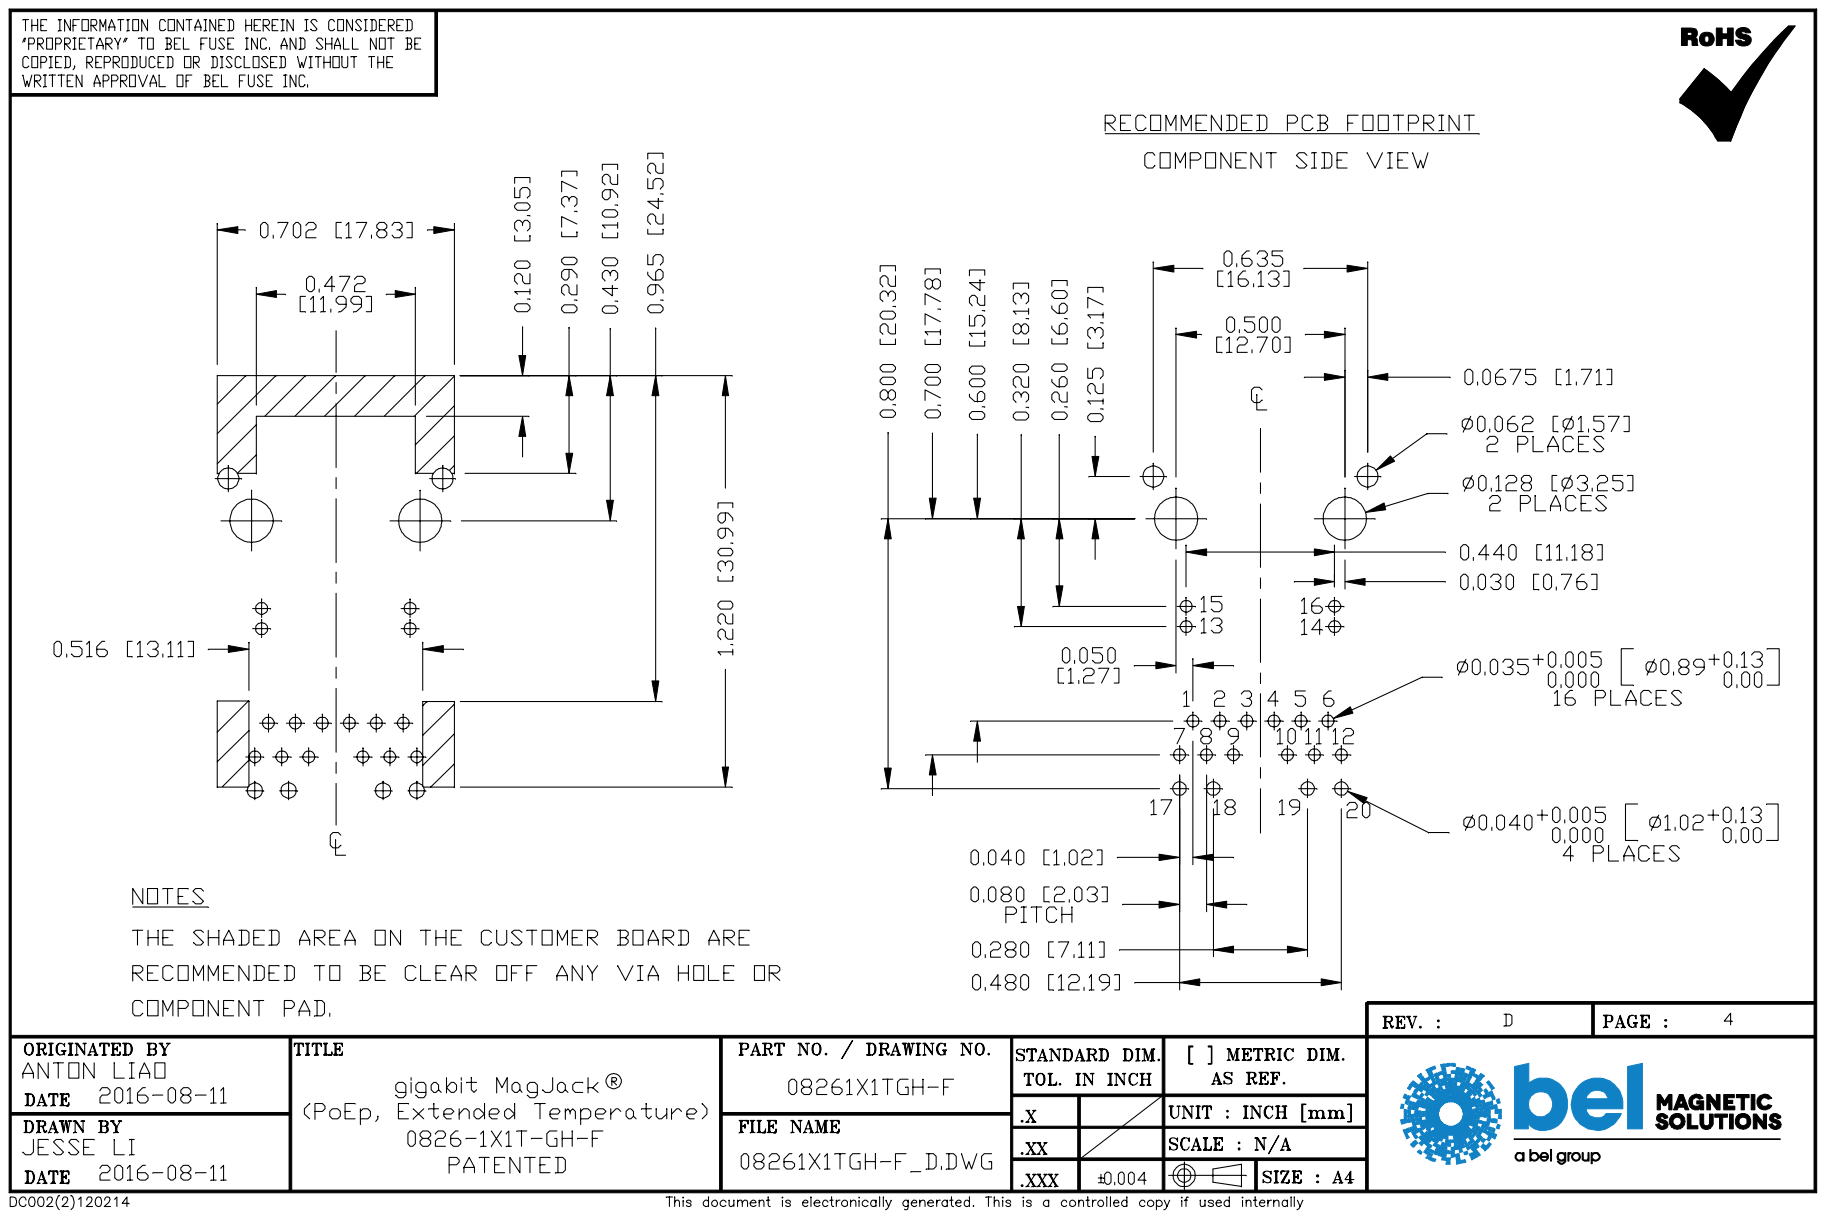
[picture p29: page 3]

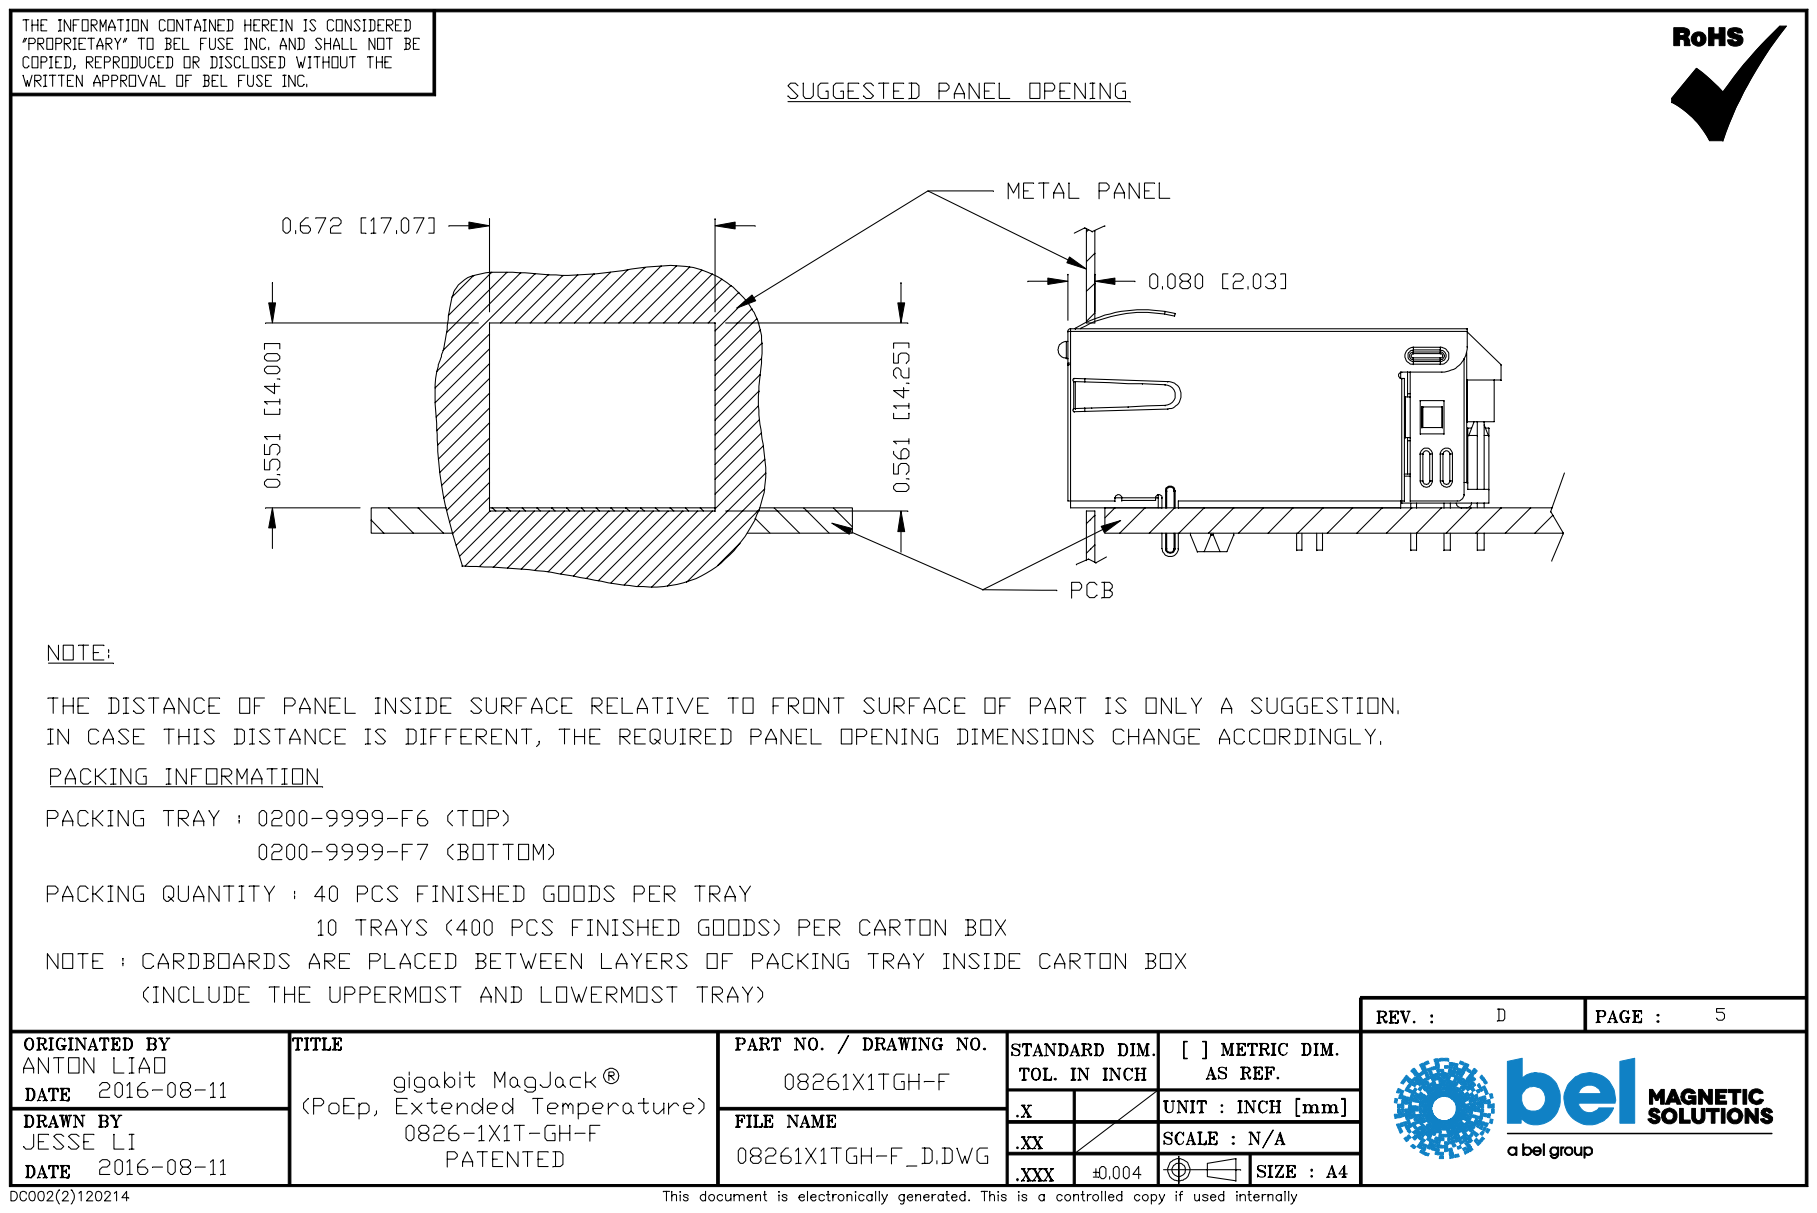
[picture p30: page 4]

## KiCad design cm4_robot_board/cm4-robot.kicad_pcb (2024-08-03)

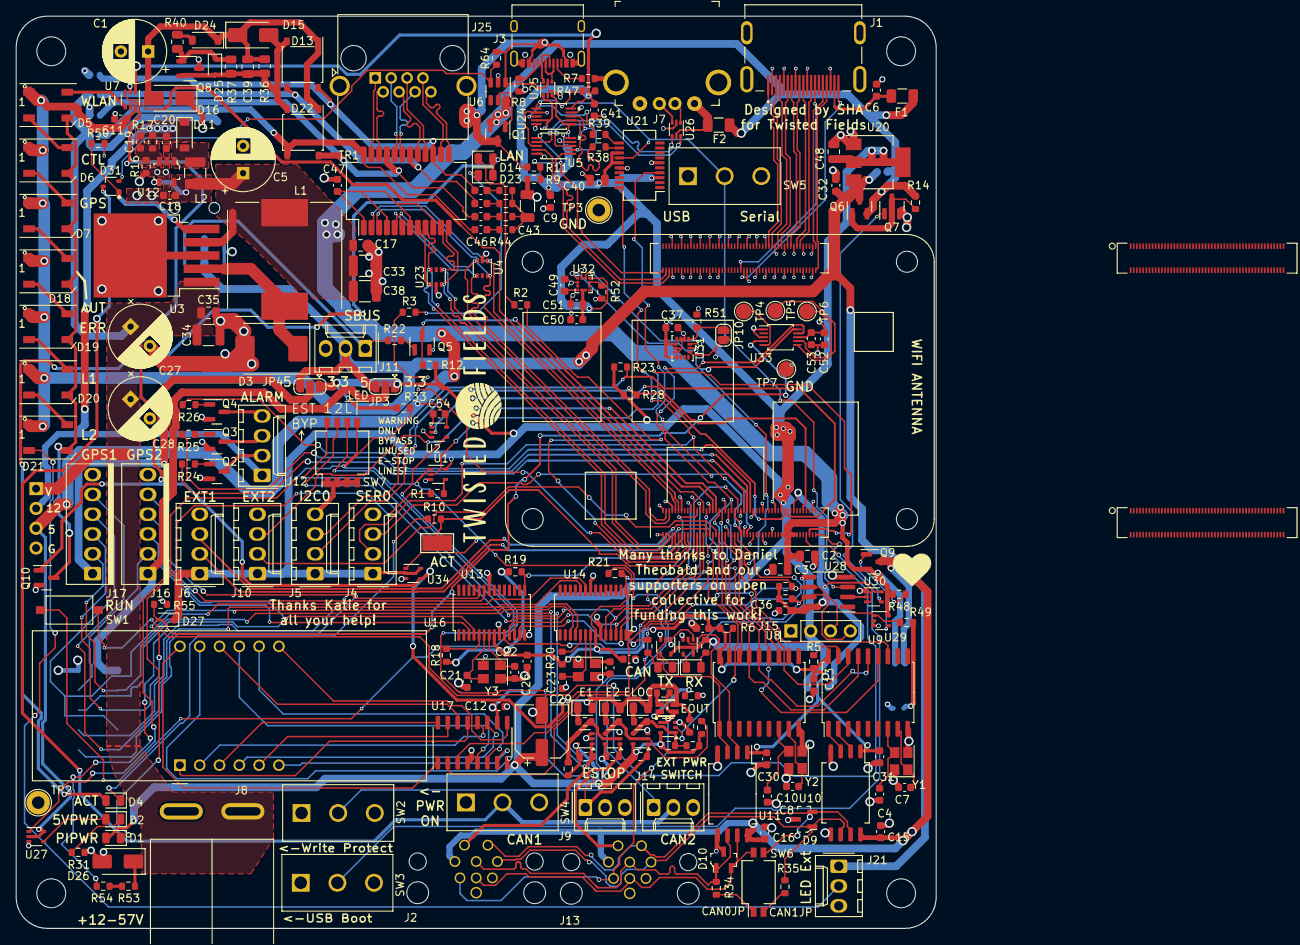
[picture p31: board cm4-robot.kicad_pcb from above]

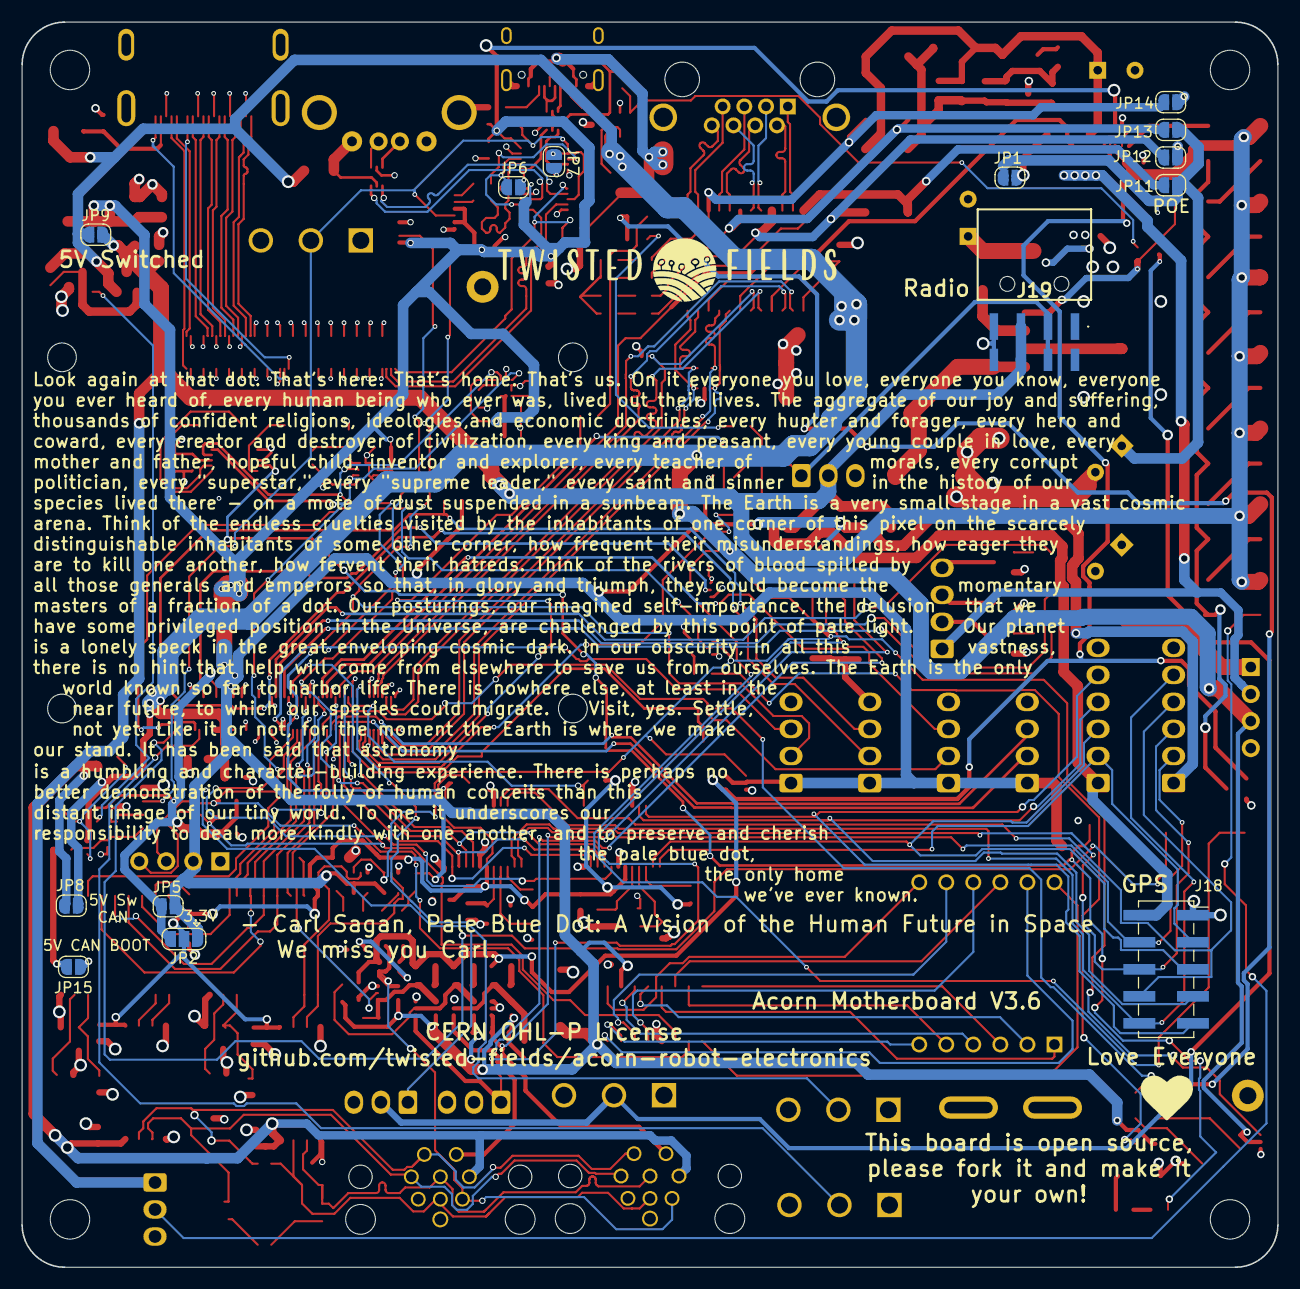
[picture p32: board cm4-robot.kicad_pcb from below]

Board: 4 copper layers, 118.0 x 117.0 mm, 262 parts (14 on the bottom side), 223 nets.

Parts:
C1, C27, C28: 47uF 63V solid; CP_Radial_D8.0mm_P3.50mm
C2, C3, C17, C48: 10uF 25V; C_0805_2012Metric
C4, C7, C8, C10: 18pF 50V; C_0603_1608Metric
C5: 1000uF 10v solid; CP_Radial_D8.0mm_P3.50mm
C6, C9, C11, C12, C13, C14, C15, C16, C25, C26, C30, C31, C36, C37, C41, C47, C49, C50, C53, C54: 0.1uF 50V; C_0603_1608Metric
C18: 4.7uF 25V; C_0603_1608Metric
C19, C21, C22, C23, C24: 22pF 50V; C_0603_1608Metric
C20: 1uF 25V; C_0603_1608Metric
C29: 470uF 10V; CP_Elec_6.3x7.7
C32, C51, C52: 1uF 50V; C_0603_1608Metric
C33, C38: 47uF 16V; C_1210_3225Metric
C34: 4.7uF 100V; C_1210_3225Metric
C35, C39: 0.1uF 100V; C_0805_2012Metric
C40: 0.1uF 50V; C_0805_2012Metric
C42, C44, C45, C46: 22nF 100v; C_0603_1608Metric
C43: 1nF 2kV; C_1206_3216Metric
D1, D17, D23: LED_YELLOW; LED_0805_2012Metric
D2, D8, D28, D29: LED_RED; LED_0805_2012Metric
D3: D_Schottky; D_SMC
D4, D12, D14: LED_GREEN; LED_0805_2012Metric
D5, D6, D7, D18, D19, D20, D21: WS2812B; LED_WS2812B_PLCC4_5.0x5.0mm_P3.2mm
D9, D10: CDSOT23-SM712; SOT-23-3
D11: MBR0530; D_SOD-123
D13, D22: ABS2; Diode_Bridge_Diotec_ABS
D15: SMAJ60A; D_SMA
D16: D; D_SMA
D24: 28V / 500mW; D_SOD-123
D25: 15V / 200mW; D_SOD-323
D26: SMAJ51A; D_SMA
D27: 1N4148WS; D_SOD-323
D30: LED_Dual_KKAA; LED-ARRAY-SMD_4P-L1.9-W1.6-BL-CW
D31: Diode Dual Common Cathode 80v maximum reverse vol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; SOT-323_SC-70
F1, F2: Polyfuse; Fuse_1206_3216Metric
H1, H2, H3, H4: MountingHole; MountingHole_3.7mm
J1: 1747981-1; TE_1747981-1
J2: CAN Interface A; M12A-08PFFR
J3: USB_C_Receptacle_USB2.0; USB_C_Receptacle_XKB_U262-16XN-4BVC11
J4, J5, J6, J10, J12: Conn_01x04; Molex_KK-254_AE-6410-04A_1x04_P2.54mm_Vertical
J7: USB HOSTING OUT; USB_A_Female_UE27AC54100
J8: Conn_01x02; PowerPole_PP45_1336G1_1x2_Horizontal
J9: ESTOP; Molex_KK-254_AE-6410-03A_1x03_P2.54mm_Vertical
J11, J21: Conn_01x03; Molex_KK-254_AE-6410-03A_1x03_P2.54mm_Vertical
J13: CAN Interface B; M12A-08PFFR
J14: Power Sw; Molex_KK-254_AE-6410-03A_1x03_P2.54mm_Vertical
J15: I2C OLED; PinHeader_1x04_P2.54mm_Vertical
J16, J17: Ckmtw-W-2510S06P_1x06_P2.54mm_Vertical
J18: Serial Rear; PinSocket_2x05_P2.54mm_Vertical_SMD
J19: SBUS; 610108249221
J22: DNP; PinHeader_1x04_P2.54mm_Vertical
J23, J24: Conn_01x01; DF40C-100DS-0.4V51
J25: RJ45; RJ45_R-RJ45R08P-B000
JP1, JP5, JP6, JP7, JP8, JP9, JP10, JP11, JP12, JP13, JP14, JP15: SolderJumper_2_Open; SolderJumper-2_P1.3mm_Open_RoundedPad1.0x1.5mm
JP2, JP3, JP4: SolderJumper_3_Open; SolderJumper-3_P1.3mm_Open_RoundedPad1.0x1.5mm
L1: 100uH; L_15mmx15mm
L2: 10uH; L_1210_3225Metric
Module1: ComputeModule4-CM4; Raspberry-Pi-4-Compute-Module
Q1: Q_PMOS_GSD; SOT-23
Q2, Q3, Q4, Q5, Q10: Q_NMOS_GSD; SOT-23
Q6, Q9: AO3401A; SOT-23
Q7: AO3400A; SOT-23
Q8: Si2328DS; SOT-23-3
R1, R10, R19, R21: 1k; R_0603_1608Metric
R2, R3: 470R; R_0603_1608Metric
R4, R9, R11, R32, R56, R57: 2.2k 1%; R_0603_1608Metric
R5, R6, R12, R14, R18, R20, R23, R28, R29, R30, R33, R47, R48, R49, R58, R61, R62, R63, R64: 10K; R_0603_1608Metric
R7, R8, R51, R52: 5.1k; R_0603_1608Metric
R13, R38, R39: 27R; R_0603_1608Metric
R15: 56R; R_0603_1608Metric
R16: 205k; R_0603_1608Metric
R17: 1.8M; R_0603_1608Metric
R22, R24, R25, R26: 100R; R_0603_1608Metric
R27, R45, R46, R59, R60: 130R; R_0603_1608Metric
R31: 200R; R_0603_1608Metric
R34, R35: 120R; R_0603_1608Metric
R36: 24k; R_0805_2012Metric
R37: 249k; R_0805_2012Metric
R40: 51k; R_0805_2012Metric
R41, R42, R43, R44: 75R 100v; R_0603_1608Metric
R50: 100k; R_0603_1608Metric
R53, R54: 50k 0.1%; R_0603_1608Metric
R55: 5.1k 0.1%; R_0603_1608Metric
SW1: B3U-1000P; SW_TS_1101_C_W
SW2, SW3, SW4, SW5: SW_SPDT; CS12ANW03
SW6: SW_DIP_x02; SW_DIP_SPSTx02_Slide_KingTek_DSHP02TS_W7.62mm_P1.27mm
SW7: CONFIG_SW; SW_DIP_SPSTx04_Slide_KingTek_DSHP04TS_W7.62mm_P1.27mm
TP1: TestPoint; TestPoint_Keystone_5019_Minature
TP2, TP3: TestPoint; TestPoint_Loop_D2.60mm_Drill1.6mm_Beaded
TP4, TP5, TP6, TP7: TestPoint; TestPoint_Pad_D2.0mm
TR1: G2401CG; Transformer_Ethernet_YDS_30F-51NL_SO-24_7.1x15.1mm
U1, U2, U15, U18, U19, U22, U27, U29, U30, U34, U35, U36: SN74LVC1G07QDCKTQ1; SOT-353_SC-70-5
U3: LM2576HVS-5; TO-263-5_TabPin3
U4, U23: TPD4E1U06DCKR; SOT-363_SC-70-6
U5, U24: ISL54222AIUZ
U6: LTC4412xS6; TSOT-23-6
U7: TXS0101DCKR; SOT-363_SC-70-6
U8, U9: MCP2515-xSO; SOIC-18W_7.5x11.6mm_P1.27mm
U10, U11: isolator; SOIC-8_7.5x5.85mm_P1.27mm
U12: TPS61040DBVR; SOT-753
U13, U14: SC16IS752; TSSOP-28_4.4x9.7mm_P0.65mm
U16: CC56-12SEKWA; CA56-12SEKWA
U17: ET6226M; SO-16_3.9x9.9mm_P1.27mm
U20: TLV1117LV33DCYR; SOT-223-3_TabPin2
U21: FT231XS; SSOP-20_3.9x8.7mm_P0.635mm
U25, U26: USBLC6-2P6; SOT-666
U28: PCA9536D; SOIC-8_3.9x4.9mm_P1.27mm
U31: LSM6DS3; LGA-14_3x2.5mm_P0.5mm_LayoutBorder3x4y
U32: LIS3MDL; LGA-12_2x2mm_P0.5mm
U33: ADS1115IDGS; TSSOP-10_3x3mm_P0.5mm
Y1, Y2: 16MHz; Crystal_SMD_3225-4Pin_3.2x2.5mm
Y3, Y4: 14.7456MHz; Crystal_SMD_3225-4Pin_3.2x2.5mm

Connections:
3.3V_5V_PI_CONTROL: U28.2 (IO1), U30.2 (A)
3.3V_PI_OUT: C36.1, JP2.3 (B), JP5.1 (A), Module1.86 (+3.3v_(Output)), R29.1, R30.1, U28.8 (VDD), U30.5 (VCC)
5V_CAN_ENABLE: R49.1, U28.1 (IO0), U29.1 (/OE)
5V_switched: C11.1, C32.1, D5.1 (VDD), D6.1 (VDD), D7.1 (VDD), D18.1 (VDD), D19.1 (VDD), D20.1 (VDD), D21.1 (VDD), J11.2, J19.5, J19.6, J21.1, JP3.3 (B), JP4.3 (B), JP9.2 (B), Q6.3 (D), U7.6 (VCCB), U20.3 (VI)
5V_switched_CAN: C15.2, C16.2, J2.7, J13.7, JP8.2 (B), Q9.3 (D), U10.8 (VCC2), U11.8 (VCC2)
+3V3: C9.2, C12.1, C29.1, C37.1, C40.1, C41.2, C48.1, C50.1, C51.1, C52.2, C53.1, D1.2 (A), D27.1 (K), J4.1, J5.1, J6.1, J10.1, J15.2, JP2.1 (A), JP3.1 (A), JP4.1 (A), JP5.2 (B), JP10.1 (A), Module1.78 (GPIO_VREF(1.8v/3.3v_Input)), R4.2, R12.1, R13.1, R15.1, R23.1, R28.1, R32.2, R33.1, R47.1, R56.2, R57.2, R61.1, R62.1, R63.1, U1.5 (VCC), U5.10 (VDD), U7.1 (VCCA), U15.5 (VCC), U17.10 (VCC), U18.5 (VCC), U19.5 (VCC), U20.2 (VO), U21.3 (VCCIO), U21.13 (3V3OUT), U21.15 (VCC), U22.5 (VCC), U24.10 (VDD), U31.5 (VDDIO), U31.8 (VDD), U31.12 (CS), U32.5 (Vdd), U32.6 (Vdd_IO), U32.10 (~CS), U33.8 (VDD), U34.2 (A), U34.5 (VCC), U35.5 (VCC), U36.5 (VCC)
+5V: C2.1, C3.1, C5.1, C17.1, C18.1, C33.1, C38.1, C54.1, F1.1, F2.2, J22.3, JP8.1 (A), JP9.1 (A), L1.2, L2.1, Module1.77 (+5v_(Input)), Module1.79 (+5v_(Input)), Module1.81 (+5v_(Input)), Module1.83 (+5v_(Input)), Module1.85 (+5v_(Input)), Module1.87 (+5v_(Input)), Q1.2 (S), Q6.2 (S), Q9.2 (S), R14.1, R48.1, U2.5 (VCC), U3.4 (FB), U6.6 (SENSE), U12.4 (EN), U12.5 (VIN), U27.2 (A), U27.5 (VCC), U29.5 (VCC)
+12V: C19.1, C20.1, D11.1 (K), J12.1, J22.2, R17.2
/5V_FUSED: F2.1, J7.1 (VBUS), U26.5 (VBUS)
/CAN0_N: D10.1 (Input), J2.8, J13.8, R34.1, U11.6 (CANL)
/CAN0_P: D10.2 (Input), J2.5, J13.5, SW6.4, U11.7 (CANH)
/CAN1_N: D9.1 (Input), J2.3, J13.3, R35.1, U10.6 (CANL)
/CAN1_P: D9.2 (Input), J2.2, J13.2, SW6.3, U10.7 (CANH)
/D0N: J25.2, TR1.22 (MX1-)
/D0P: J25.1, TR1.23 (MX1+)
/D1N: J25.6, TR1.19 (MX2-)
/D1P: J25.3, TR1.20 (MX2+)
/D2N: J25.5, TR1.16 (MX3-)
/D2P: J25.4, TR1.17 (MX3+)
/D3N: J25.8, TR1.13 (MX4-)
/D3P: J25.7, TR1.14 (MX4+)
/ESTOP_SINK_ALL: R27.2, R57.1, R63.2, U35.4 (Y), U36.1 (/OE)
/HDMI0_CEC: J1.13 (CEC), Module1.151 (HDMI0_CEC)
/HDMI0_CK_N: J1.12 (CK-), Module1.190 (HDMI0_CLK_N)
/HDMI0_CK_P: J1.10 (CK+), Module1.188 (HDMI0_CLK_P)
/HDMI0_D0_N: J1.9 (D0-), Module1.184 (HDMI0_TX0_N)
/HDMI0_D0_P: J1.7 (D0+), Module1.182 (HDMI0_TX0_P)
/HDMI0_D1_N: J1.6 (D1-), Module1.178 (HDMI0_TX1_N)
/HDMI0_D1_P: J1.4 (D1+), Module1.176 (HDMI0_TX1_P)
/HDMI0_D2_N: J1.3 (D2-), Module1.172 (HDMI0_TX2_N)
/HDMI0_D2_P: J1.1 (D2+), Module1.170 (HDMI0_TX2_P)
/HDMI0_HOTPLUG: J1.19 (HPD/HEAC-), Module1.153 (HDMI0_HOTPLUG)
/HDMI0_SCL: J1.15 (SCL), Module1.200 (HDMI0_SCL)
/HDMI0_SDA: J1.16 (SDA), Module1.199 (HDMI0_SDA)
/HDMI_5v: C6.1, F1.2, J1.18 (+5V)
/LED_3.3V_POWER_NONINV: D8.2 (A), D28.2 (A), D29.2 (A), D30.3 (A1), Q10.1 (G), R58.2, U7.5 (OE), U34.4 (Y)
/LED_3.3V_POWER_SW: D4.2 (A), D14.2 (A), D23.2 (A)
/RX1: J16.3, J18.5, U13.4 (RXA)
/RX2: J16.5, J18.9, U13.24 (RXB)
/RX3: J17.3, J18.6, U14.4 (RXA)
/RX4: J17.5, J18.10, U14.24 (RXB)
/TX1: J16.2, J18.3, U13.3 (TXA)
/TX2: J16.4, J18.7, U13.23 (TXB)
/TX3: J17.2, J18.4, U14.3 (TXA)
/TX4: J17.4, J18.8, U14.23 (TXB)
/USB_DN: R38.2, U21.12 (USBDM)
/USB_DP: R39.2, U21.11 (USBDP)
/VMEAS: D27.2 (A), R54.2, R55.1, U33.4 (AIN0)
//LED_EN: R33.2, SW7.5, U1.1 (/OE), U18.1 (/OE), U19.1 (/OE), U27.1 (/OE), U34.1 (/OE)
/~5V_EN: D31.3 (K), J14.2, SW4.2 (B)
/~VBUS_5V_ENA: D31.2 (A), R64.1, U6.3 (CTL)
/~VIN_5V_EN: D31.1 (A), R50.2, U3.5 (~ON/OFF)
A1: Module1.54 (GPIO4), R24.1
A2: Module1.56 (GPIO3), R25.1
A3: Module1.58 (GPIO2), R26.1
CAN_CIPO: Module1.44 (GPIO10), U8.14 (SI), U9.14 (SI)
CAN_COPI: Module1.40 (GPIO9), U8.15 (SO), U9.15 (SO)
CAN_CS0: Module1.39 (GPIO8), U8.16 (~CS)
CAN_CS1: Module1.37 (GPIO7), U9.16 (~CS)
CAN_SCI0: Module1.41 (GPIO25), U8.12 (~INT)
CAN_SCI1: Module1.45 (GPIO24), U9.12 (~INT)
CAN_SCK: Module1.38 (GPIO11), U8.13 (SCK), U9.13 (SCK)
CS1: Module1.49 (GPIO18), U13.10 (A0/~CS)
CS2: Module1.50 (GPIO17), U14.10 (A0/~CS)
EEPROM_nWP: Module1.20 (EEPROM_nWP), SW2.2 (B)
ESTOP: Module1.30 (GPIO6), U36.2 (A)
ESTOP_OUT: D30.4 (A2), J2.6, J13.6, R60.2, U36.4 (Y)
ESTOP_SINK1: J2.1, R32.1, SW7.8, U22.1 (/OE)
ESTOP_SINK2: J13.1, R4.1, SW7.7, U15.1 (/OE)
ESTOP_SINK_LOCAL: J9.1, R56.1, SW7.6, U35.1 (/OE)
ETH_LEDG: Module1.17 (Ethernet_nLED2(3.3v)), R3.2
ETH_LEDY: Module1.15 (Ethernet_nLED3(3.3v)), R2.2
EXTRA_1_GPIO16: J6.2, Module1.29 (GPIO16)
EXTRA_2_GPIO12: J6.3, Module1.31 (GPIO12)
EXTRA_3_GPIO1: J10.2, Module1.35 (ID_SC)
EXTRA_4_GPIO0: J10.3, Module1.36 (ID_SD)
EXTRA_GPIO: J14.1, U28.5 (IO3)
FB: C19.2, R16.2, R17.1, U12.3 (FB)
GLOBAL_EN: Module1.99 (Global_EN), SW1.2
GND: C1.2, C2.2, C3.2, C4.2, C5.2, C6.2, C7.2, C8.2, C9.1, C10.2, C11.2, C12.2, C13.1, C14.1, C15.1, C16.1, C17.2, C18.2, C20.2, C21.1, C22.2, C23.1, C24.2, C25.1, C26.1, C27.2, C28.2, C29.2, C30.2, C31.2, C32.2, C33.2, C34.2, C35.2, C36.2, C37.2, C38.2, C40.2, C41.1, C43.2, C47.1, C48.2, C49.2, C50.2, C51.2, C52.1, C53.2, C54.2, D3.2 (A), D9.3 (Output), D10.3 (Output), D26.2 (A2), J1.2 (D2S), J1.5 (D1S), J1.8 (D0S), J1.11 (CKS), J1.17 (GND), J1.SH1 (SH), J1.SH2 (SH), J1.SH3 (SH), J1.SH4 (SH), J2.4, J2.9, J3.A1 (GND), J3.A12 (GND), J3.B1 (GND), J3.B12 (GND), J3.S1 (SHIELD), J4.4, J5.4, J6.4, J7.4 (GND), J7.SH (Shield), J8.2, J9.3, J10.4, J11.3, J13.4, J13.9, J14.3, J15.1, J16.6, J17.6, J18.1, J19.7, J19.8, J21.3, J22.4, J24.1, JP12.1 (A), JP14.1 (A), JP15.2 (B), Module1.1 (GND), Module1.2 (GND), Module1.7 (GND), Module1.8 (GND), Module1.13 (GND), Module1.14 (GND), Module1.22 (GND), Module1.23 (GND), Module1.32 (GND), Module1.33 (GND), Module1.42 (GND), Module1.43 (GND), Module1.52 (GND), Module1.53 (GND), Module1.59 (GND), Module1.60 (GND), Module1.65 (GND), Module1.66 (GND), Module1.71 (GND), Module1.74 (GND), Module1.98 (GND), Module1.107 (GND), Module1.108 (GND), Module1.113 (GND), Module1.114 (GND), Module1.119 (GND), Module1.120 (GND), Module1.125 (GND), Module1.126 (GND), Module1.131 (GND), Module1.132 (GND), Module1.137 (GND), Module1.138 (GND), Module1.144 (GND), Module1.150 (GND), Module1.155 (GND), Module1.156 (GND), Module1.161 (GND), Module1.162 (GND), Module1.167 (GND), Module1.168 (GND), Module1.173 (GND), Module1.174 (GND), Module1.179 (GND), Module1.180 (GND), Module1.185 (GND), Module1.186 (GND), Module1.191 (GND), Module1.192 (GND), Module1.197 (GND), Module1.198 (GND), Q2.2 (S), Q3.2 (S), Q4.2 (S), Q5.2 (S), Q7.2 (S), Q8.3 (D), Q10.2 (S), R7.1, R8.2, R9.2, R16.1, R31.1, R51.1, R52.1, R55.2, R58.1, R59.2, SW2.1 (A), SW3.1 (A), SW4.1 (A), SW5.1 (A), SW7.1, SW7.2, SW7.3, SW7.4, TP2.1, TP3.1, TP7.1, U1.3 (GND), U2.1 (/OE), U2.3 (GND), U3.3 (GND), U4.2 (VN), U5.5 (GND), U5.9 (*OE), U6.2 (GND), U7.2 (GND), U8.9 (VSS), U9.9 (VSS), U10.4 (GND1), U10.5 (GND2), U11.4 (GND1), U11.5 (GND2), U12.2 (GND), U13.9 (I2C/~SPI), U13.14 (SDA/VSS), U13.22 (VSS), U14.9 (I2C/~SPI), U14.14 (SDA/VSS), U14.22 (VSS), U15.3 (GND), U17.4 (GND), U18.3 (GND), U19.3 (GND), U20.1 (GND), U21.6 (GND), U21.16 (GND), U22.2 (A), U22.3 (GND), U23.2 (VN), U24.5 (GND), U24.9 (*OE), U25.2 (GND), U26.2 (GND), U27.3 (GND), U28.4 (VSS), U29.2 (A), U29.3 (GND), U30.1 (/OE), U30.3 (GND), U31.2 (SDX), U31.3 (SCX), U31.6 (GND), U31.7 (GND), U32.2 (GND), U32.3 (GND), U32.12 (GND), U33.1 (ADDR), U33.3 (GND), U34.3 (GND), U35.3 (GND), U36.3 (GND), Y1.2, Y1.4, Y2.2, Y2.4, Y3.2, Y3.4, Y4.2, Y4.4
GR1: U16.12 (CC1), U17.1 (GR1)
GR2: U16.9 (CC2), U17.5 (GR2)
GR3: U16.8 (CC3), U17.6 (GR3)
GR4: U16.6 (CC4), U17.7 (GR4)
IRQ1: Module1.24 (GPIO26), R19.1, U13.15 (~IRQ)
IRQ2: Module1.48 (GPIO27), R21.1, U14.15 (~IRQ)
KP: U16.3 (DPX), U17.16 (DP/KP)
KS1: U16.11 (a), U17.8 (SG1/KS1)
KS2: U16.7 (b), U17.9 (SG2/KS2)
KS3: U16.4 (c), U17.11 (SG3/KS3)
KS4: U16.2 (d), U17.12 (SG4/KS4)
KS5: U16.1 (e), U17.13 (SG5/KS5)
KS6: U16.10 (f), U17.14 (SG6/KS6)
KS7: U16.5 (g), U17.15 (SG7/KS7)
unnamed: C42.2, R41.1
unnamed: C43.1, R41.2, R42.2, R43.2, R44.2
unnamed: C44.2, R42.1
unnamed: C45.2, R43.1
unnamed: C46.2, R44.1
unnamed: C47.2, TR1.1 (CT), TR1.4 (CT), TR1.7 (CT), TR1.10 (CT)
unnamed: D1.1 (K), R1.1
unnamed: D2.2 (A), U27.4 (Y)
unnamed: D2.1 (K), R31.2
unnamed: D3.1 (K), L1.1, U3.2 (OUT)
unnamed: D4.1 (K), R10.2
unnamed: D5.4 (DIN), U7.4 (B)
unnamed: D5.2 (DOUT), D6.4 (DIN)
unnamed: D6.2 (DOUT), D7.4 (DIN)
unnamed: D8.1 (K), R27.1
unnamed: D11.2 (A), L2.2, U12.1 (SW)
unnamed: D12.2 (A), R13.2
unnamed: D12.1 (K), U18.4 (Y)
unnamed: D14.1 (K), R2.1
unnamed: D16.1 (K), JP1.1 (A)
unnamed: D17.2 (A), R15.2
unnamed: D17.1 (K), U19.4 (Y)
unnamed: D7.2 (DOUT), D18.4 (DIN)
unnamed: D18.2 (DOUT), D19.4 (DIN)
unnamed: D5.3 (VSS), D6.3 (VSS), D7.3 (VSS), D18.3 (VSS), D19.3 (VSS), D20.3 (VSS), D21.3 (VSS), Q10.3 (D)
unnamed: D19.2 (DOUT), D20.4 (DIN)
unnamed: D20.2 (DOUT), D21.4 (DIN)
unnamed: D21.2 (DOUT), J21.2
unnamed: D23.1 (K), R3.1
unnamed: D24.2 (A), R40.2
unnamed: D25.1 (K), Q8.1 (G), R37.2, R40.1
unnamed: D28.1 (K), R45.1
unnamed: D29.1 (K), R46.1
unnamed: D30.1 (K1), R59.1
unnamed: D30.2 (K2), R60.1
unnamed: J3.A5 (CC1), R7.2
unnamed: J3.B5 (CC2), R8.1
unnamed: J12.2, Q2.3 (D)
unnamed: J12.3, Q3.3 (D)
unnamed: J12.4, Q4.3 (D)
unnamed: JP10.2 (B), R51.2, U31.1 (SDO/SA0)
unnamed: JP15.1 (A), R49.2
unnamed: Q1.1 (G), U6.5 (GATE)
unnamed: Q2.1 (G), R24.2
unnamed: Q3.1 (G), R25.2
unnamed: Q4.1 (G), R26.2
unnamed: Q5.1 (G), R22.2
unnamed: Q6.1 (G), Q7.3 (D), R14.2
unnamed: Q7.1 (G), U30.4 (Y)
unnamed: Q9.1 (G), R48.2, U29.4 (Y)
unnamed: R34.2, SW6.1
unnamed: R35.2, SW6.2
unnamed: R53.2, R54.1
unnamed: R1.2, U1.4 (Y)
unnamed: SW1.1, U2.4 (Y)
unnamed: C10.1, U8.8 (OSC1), Y2.1
unnamed: C8.1, U8.7 (OSC2), Y2.3
unnamed: R6.1, U8.17 (~RESET)
unnamed: C7.1, U9.8 (OSC1), Y1.1
unnamed: C4.1, U9.7 (OSC2), Y1.3
unnamed: R5.1, U9.17 (~RESET)
unnamed: U9.2 (RXCAN), U10.2 (RXD)
unnamed: U9.1 (TXCAN), U10.3 (TXD)
unnamed: C21.2, U13.6 (XTAL1), Y3.3
unnamed: C22.1, U13.7 (XTAL2), Y3.1
unnamed: R18.1, U13.5 (~RESET)
unnamed: C23.2, U14.6 (XTAL1), Y4.3
unnamed: C24.1, U14.7 (XTAL2), Y4.1
unnamed: R20.1, U14.5 (~RESET)
unnamed: R46.2, R61.2, U15.2 (A), U22.4 (Y)
unnamed: R45.2, R62.2, U15.4 (Y), U35.2 (A)
unnamed: C49.1, U32.4 (C1)
unnamed: R52.2, U32.9 (SDO/SA1)
unnamed: TP4.1, U33.5 (AIN1)
unnamed: TP5.1, U33.6 (AIN2)
unnamed: TP6.1, U33.7 (AIN3)
PI_n_LED_ACT: Module1.21 (PI_nLED_Activity), R10.1, TP1.1
RC_SBUS: J11.1, J19.3, J19.4, R22.1
RUN_PG: Module1.92 (RUN_PG), U2.2 (A)
RXLED: U8.2 (RXCAN), U11.2 (RXD), U19.2 (A)
RX_GPIO15: J4.2, Module1.51 (GPIO15), U21.20 (TXD)
SBUS_RX: Module1.34 (GPIO5), Q5.3 (D), R12.2
SCL0_GPIO45: J5.2, Module1.80 (SCL0), R28.2
SCL6: J15.3, Module1.47 (GPIO23), R29.2, U17.2 (CLK), U28.6 (SCL), U31.13 (SCL), U32.1 (SCL/SPC), U33.10 (SCL)
SDA0_GPIO44: J5.3, Module1.82 (SDA0), R23.2
SDA6: J15.4, Module1.46 (GPIO22), R30.2, U17.3 (DAT), U28.7 (SDA), U31.14 (SDA), U32.11 (SDA/SDI/SDO), U33.9 (SDA)
SERIALPWR1: J16.1, J18.2, JP3.2 (C)
SERIALPWR2: J17.1, JP4.2 (C)
SERIAL_CAN_PWR_3.3V: C13.2, C14.2, C25.2, C26.2, C30.1, C31.1, JP2.2 (C), R5.2, R6.2, R18.2, R19.2, R20.2, R21.2, U8.18 (VDD), U9.18 (VDD), U10.1 (VCC1), U11.1 (VCC1), U13.8 (VDD), U14.8 (VDD)
SERIAL_CIPO: Module1.26 (GPIO19), U13.12 (SO), U14.12 (SO)
SERIAL_CLK: Module1.25 (GPIO21), U13.13 (SCL/SCLK), U14.13 (SCL/SCLK)
SERIAL_COPI: Module1.27 (GPIO20), U13.11 (A1/SI), U14.11 (A1/SI)
SER_SELECT: R47.2, SW5.2 (B), U21.14 (~RESET), U24.1 (SEL), U28.3 (IO2)
TRD0_N: Module1.10 (Ethernet_Pair0_N), TR1.3 (TD1-), U4.6 (CH4)
TRD0_P: Module1.12 (Ethernet_Pair0_P), TR1.2 (TD1+), U4.1 (CH1)
TRD1_N: Module1.6 (Ethernet_Pair1_N), TR1.6 (TD2-), U4.3 (CH2)
TRD1_P: Module1.4 (Ethernet_Pair1_P), TR1.5 (TD2+), U4.4 (CH3)
TRD2_N: Module1.9 (Ethernet_Pair2_N), TR1.9 (TD3-), U23.6 (CH4)
TRD2_P: Module1.11 (Ethernet_Pair2_P), TR1.8 (TD3+), U23.1 (CH1)
TRD3_N: Module1.5 (Ethernet_Pair3_N), TR1.12 (TD4-), U23.3 (CH2)
TRD3_P: Module1.3 (Ethernet_Pair3_P), TR1.11 (TD4+), U23.4 (CH3)
TXLED: U8.1 (TXCAN), U11.3 (TXD), U18.2 (A)
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

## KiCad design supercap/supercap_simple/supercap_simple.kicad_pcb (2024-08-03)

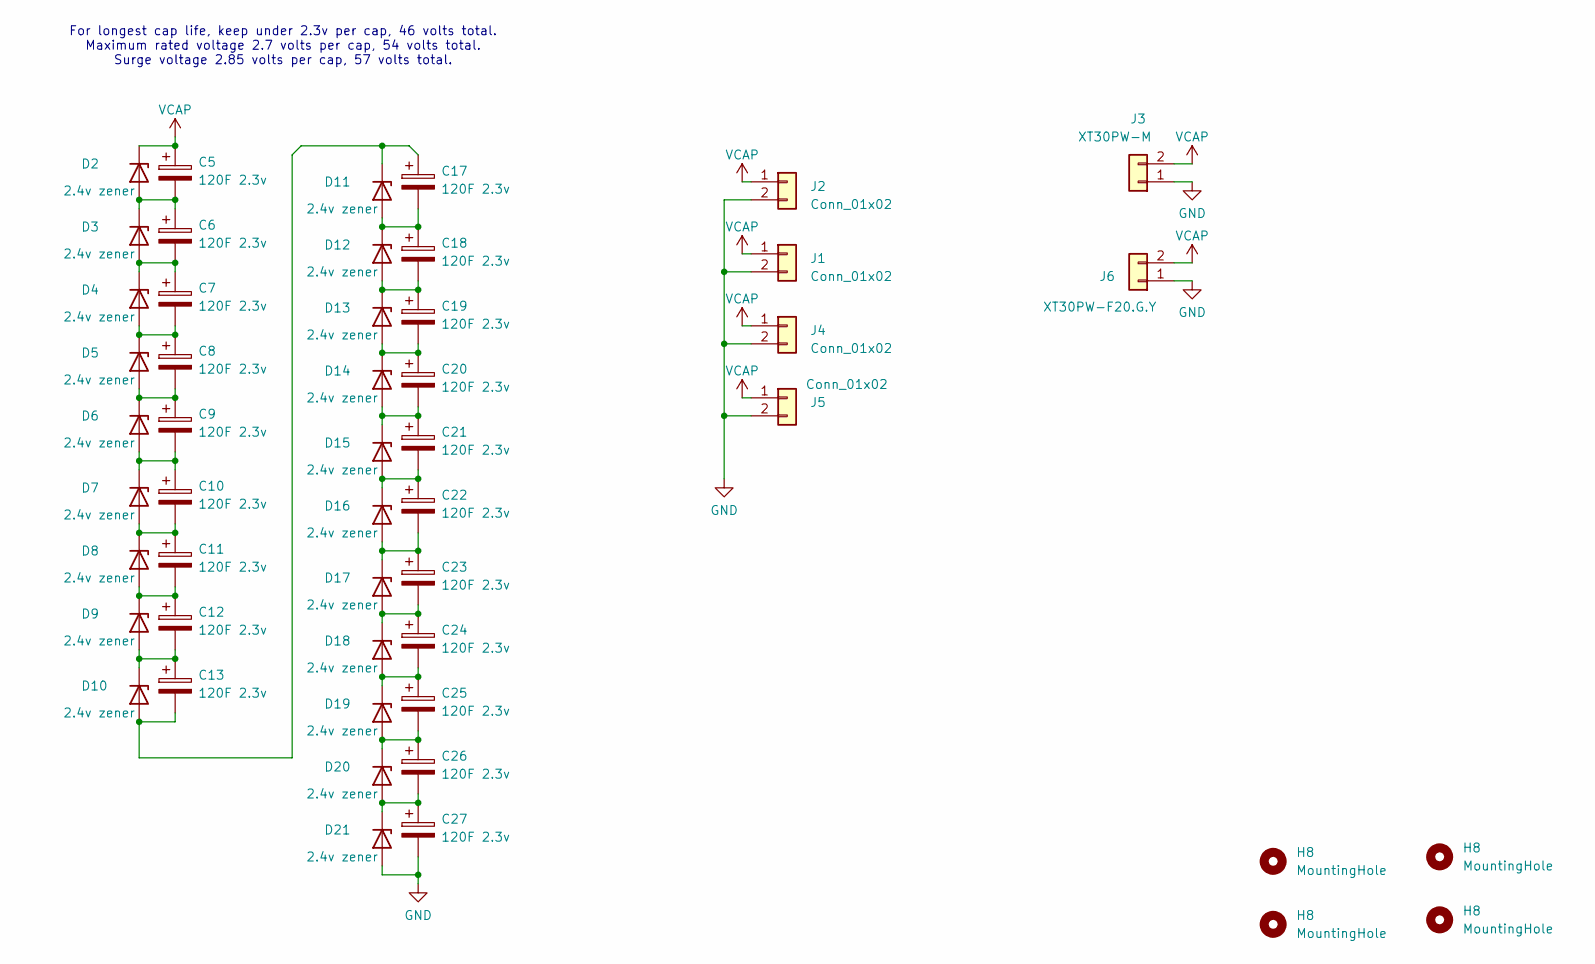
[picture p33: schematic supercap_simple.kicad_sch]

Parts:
C5, C6, C7, C8, C9, C10, C11, C12, C13, C17, C18, C19, C20, C21, C22, C23, C24, C25, C26, C27: 120F 2.3v; CP_Radial_D18.0mm_P7.50mm; Digikey 2085-TPLH-2R7/120WR18X60-ND
D2, D3, D4, D5, D6, D7, D8, D9, D10, D11, D12, D13, D14, D15, D16, D17, D18, D19, D20, D21: 2.4v zener; DIO_PESD5V0S1UL_315; LCSC C551192
H8: MountingHole; MountingHole_3.9mm_Plastite_#6
J1, J2, J4, J5: Conn_01x02; PowerPole_PP45_1336G1_1x2_Horizontal
J3: XT30PW-M; AMASS_XT30PW-M_1x02_P2.50mm_Horizontal; LCSC C431092
J6: XT30PW-F20.G.Y; AMASS_XT30PW-F_1x02_P2.50mm_Horizontal; LCSC C2913282

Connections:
GND: C27.2, D21.2 (A), J1.2, J2.2, J3.1, J4.2, J5.2, J6.1
unnamed: C5.2, C6.1, D2.2 (A), D3.1 (K)
unnamed: C6.2, C7.1, D3.2 (A), D4.1 (K)
unnamed: C7.2, C8.1, D4.2 (A), D5.1 (K)
unnamed: C8.2, C9.1, D5.2 (A), D6.1 (K)
unnamed: C9.2, C10.1, D6.2 (A), D7.1 (K)
unnamed: C10.2, C11.1, D7.2 (A), D8.1 (K)
unnamed: C11.2, C12.1, D8.2 (A), D9.1 (K)
unnamed: C13.2, C17.1, D10.2 (A), D11.1 (K)
unnamed: C12.2, C13.1, D9.2 (A), D10.1 (K)
unnamed: C17.2, C18.1, D11.2 (A), D12.1 (K)
unnamed: C18.2, C19.1, D12.2 (A), D13.1 (K)
unnamed: C19.2, C20.1, D13.2 (A), D14.1 (K)
unnamed: C20.2, C21.1, D14.2 (A), D15.1 (K)
unnamed: C21.2, C22.1, D15.2 (A), D16.1 (K)
unnamed: C22.2, C23.1, D16.2 (A), D17.1 (K)
unnamed: C23.2, C24.1, D17.2 (A), D18.1 (K)
unnamed: C24.2, C25.1, D18.2 (A), D19.1 (K)
unnamed: C25.2, C26.1, D19.2 (A), D20.1 (K)
unnamed: C26.2, C27.1, D20.2 (A), D21.1 (K)
VCAP: C5.1, D2.1 (K), J1.1, J2.1, J3.2, J4.1, J5.1, J6.2

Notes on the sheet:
For longest cap life, keep under 2.3v per cap, 46 volts total. Maximum rated voltage 2.7 volts per cap, 54 volts total. Surge voltage 2.85 volts per cap, 57 volts total.

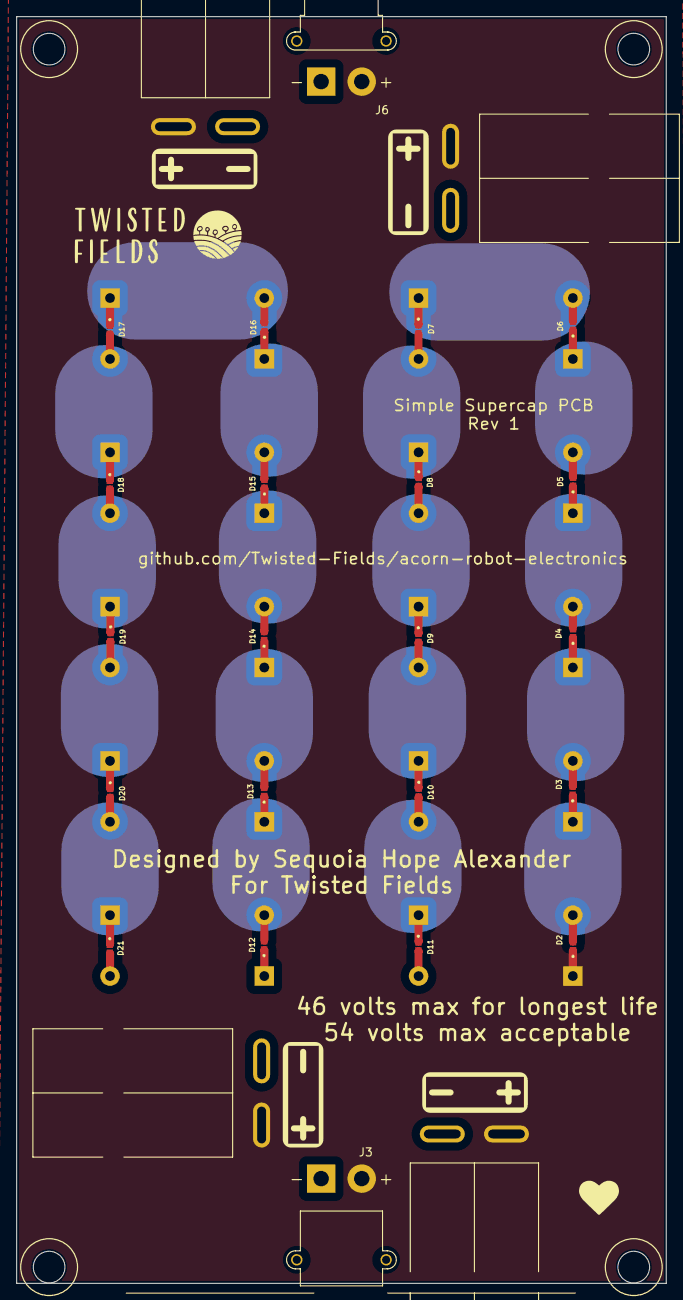
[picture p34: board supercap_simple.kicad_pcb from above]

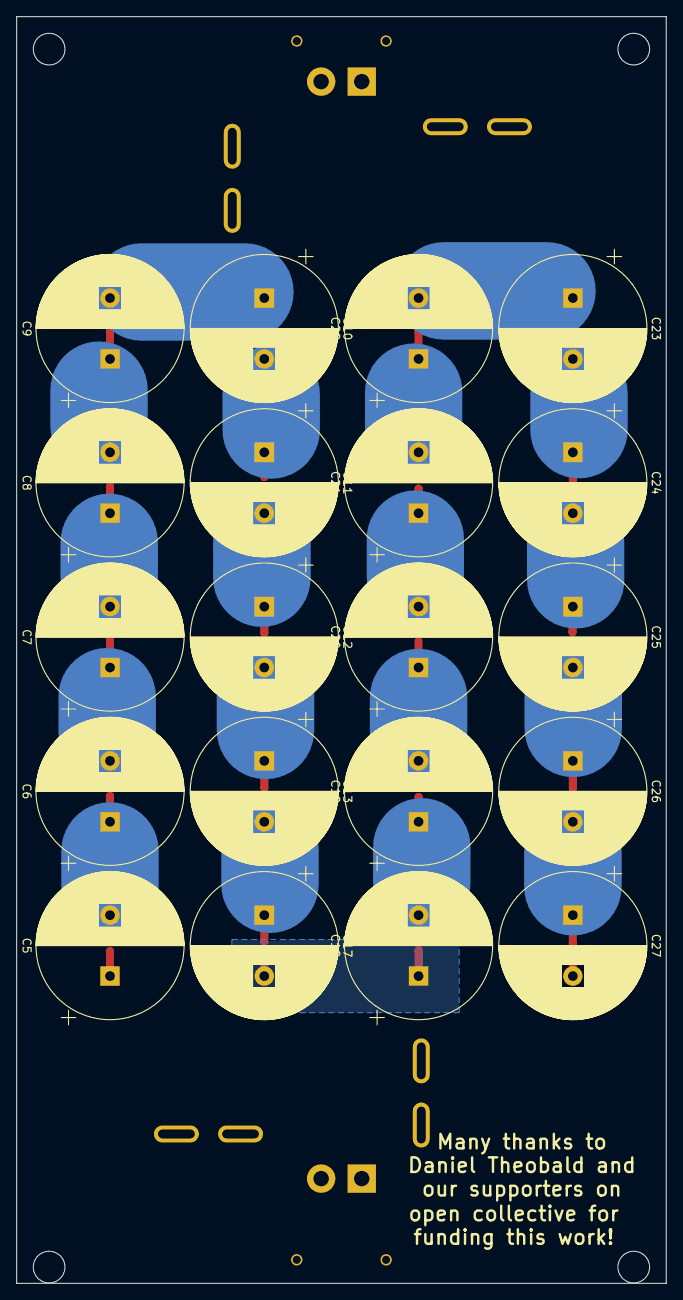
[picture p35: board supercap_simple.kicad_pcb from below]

Board: 4 copper layers, 80.0 x 156.0 mm, 50 parts (20 on the bottom side), 21 nets.

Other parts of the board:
H1, H2, H3, H4: MountingHole; MountingHole_3.9mm_Plastite_#6

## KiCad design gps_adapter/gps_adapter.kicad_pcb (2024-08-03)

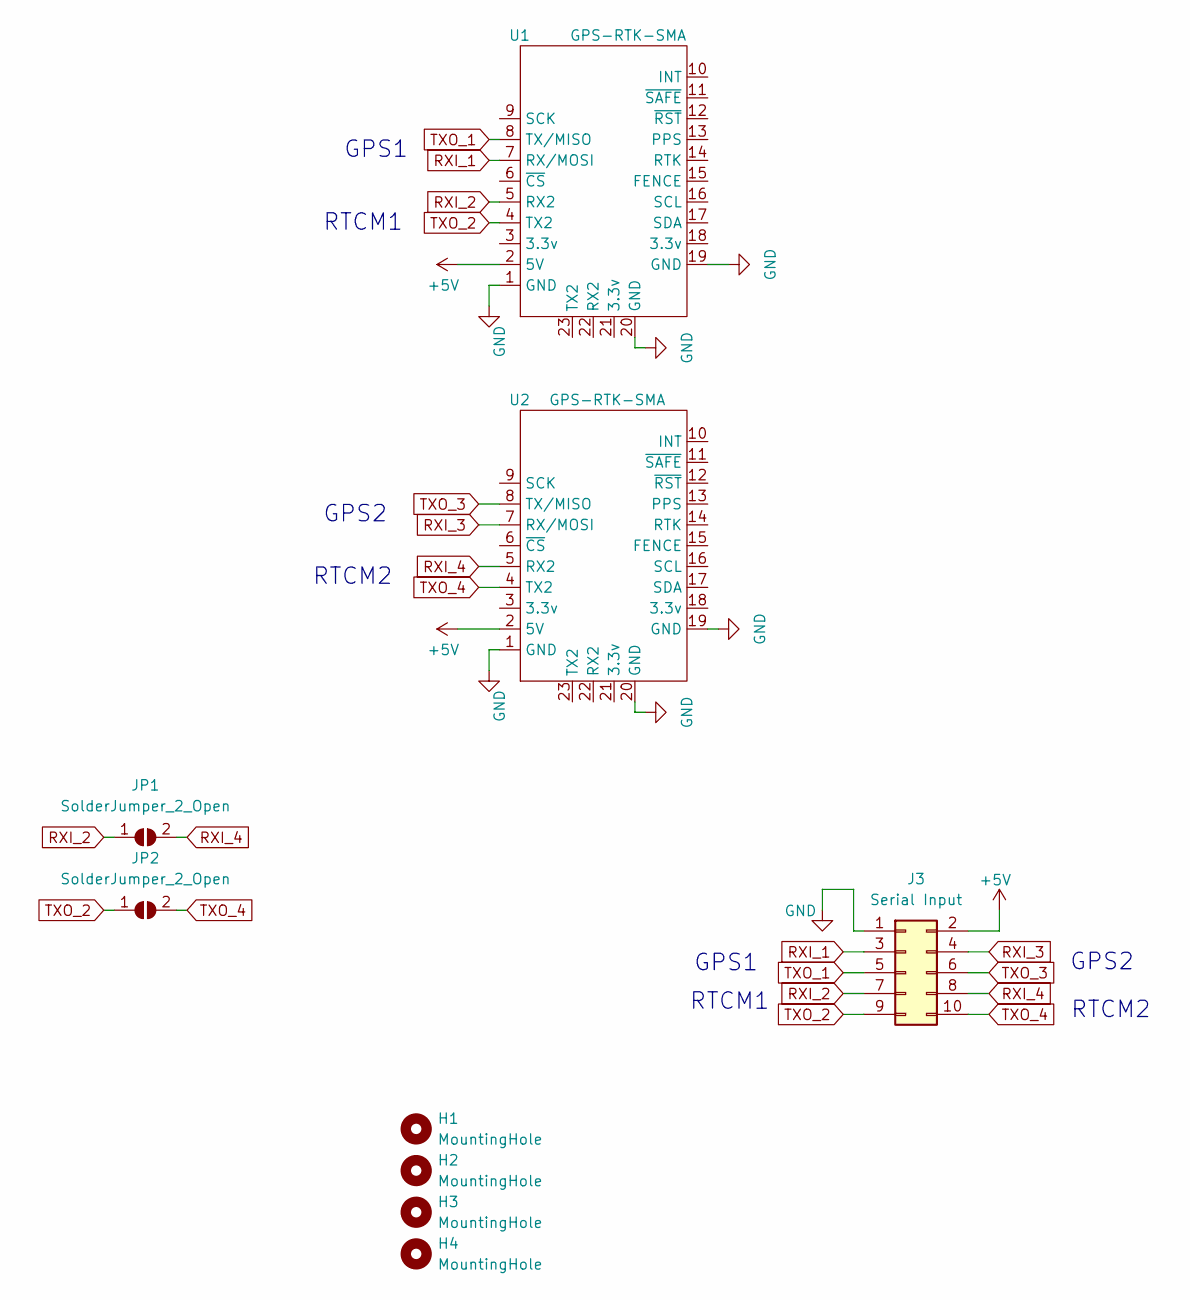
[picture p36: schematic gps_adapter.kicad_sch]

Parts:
H1, H2, H3, H4: MountingHole; MountingHole_3.7mm
J3: Serial Input; PinHeader_2x05_P2.54mm_Vertical
JP1, JP2: SolderJumper_2_Open; SolderJumper-2_P1.3mm_Open_RoundedPad1.0x1.5mm
U1, U2: GPS-RTK-SMA

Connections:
+5V: J3.2, U1.2 (5V), U2.2 (5V)
GND: J3.1, U1.1 (GND), U1.19 (GND), U1.20 (GND), U2.1 (GND), U2.19 (GND), U2.20 (GND)
RXI_1: J3.3, U1.7 (RX/MOSI)
RXI_2: J3.7, JP1.1 (A), U1.5 (RX2)
RXI_3: J3.4, U2.7 (RX/MOSI)
RXI_4: J3.8, JP1.2 (B), U2.5 (RX2)
TXO_1: J3.5, U1.8 (TX/MISO)
TXO_2: J3.9, JP2.1 (A), U1.4 (TX2)
TXO_3: J3.6, U2.8 (TX/MISO)
TXO_4: J3.10, JP2.2 (B), U2.4 (TX2)

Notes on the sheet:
GPS2
GPS1
RTCM2
RTCM1

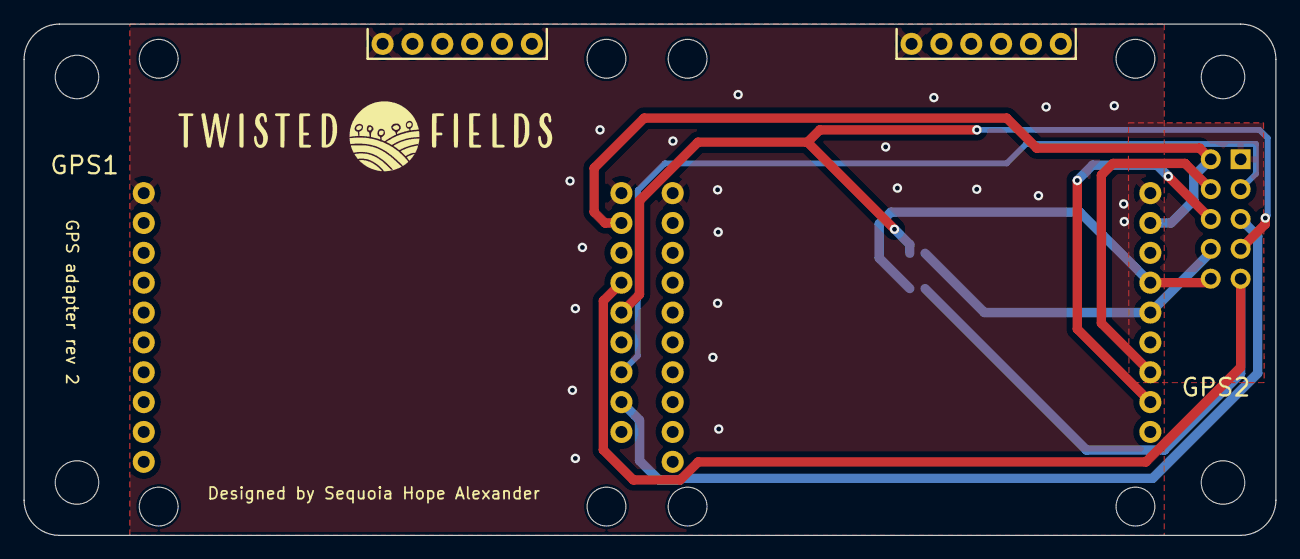
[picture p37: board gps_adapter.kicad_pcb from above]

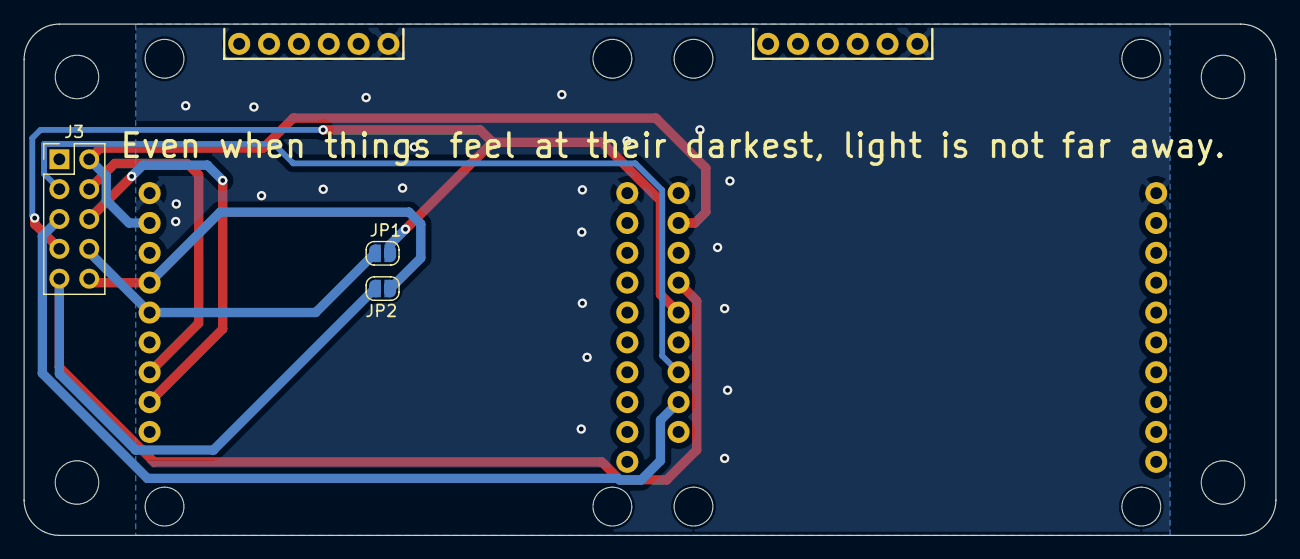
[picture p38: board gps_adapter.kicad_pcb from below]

Board: 2 copper layers, 106.5 x 43.5 mm, 9 parts (3 on the bottom side), 10 nets.

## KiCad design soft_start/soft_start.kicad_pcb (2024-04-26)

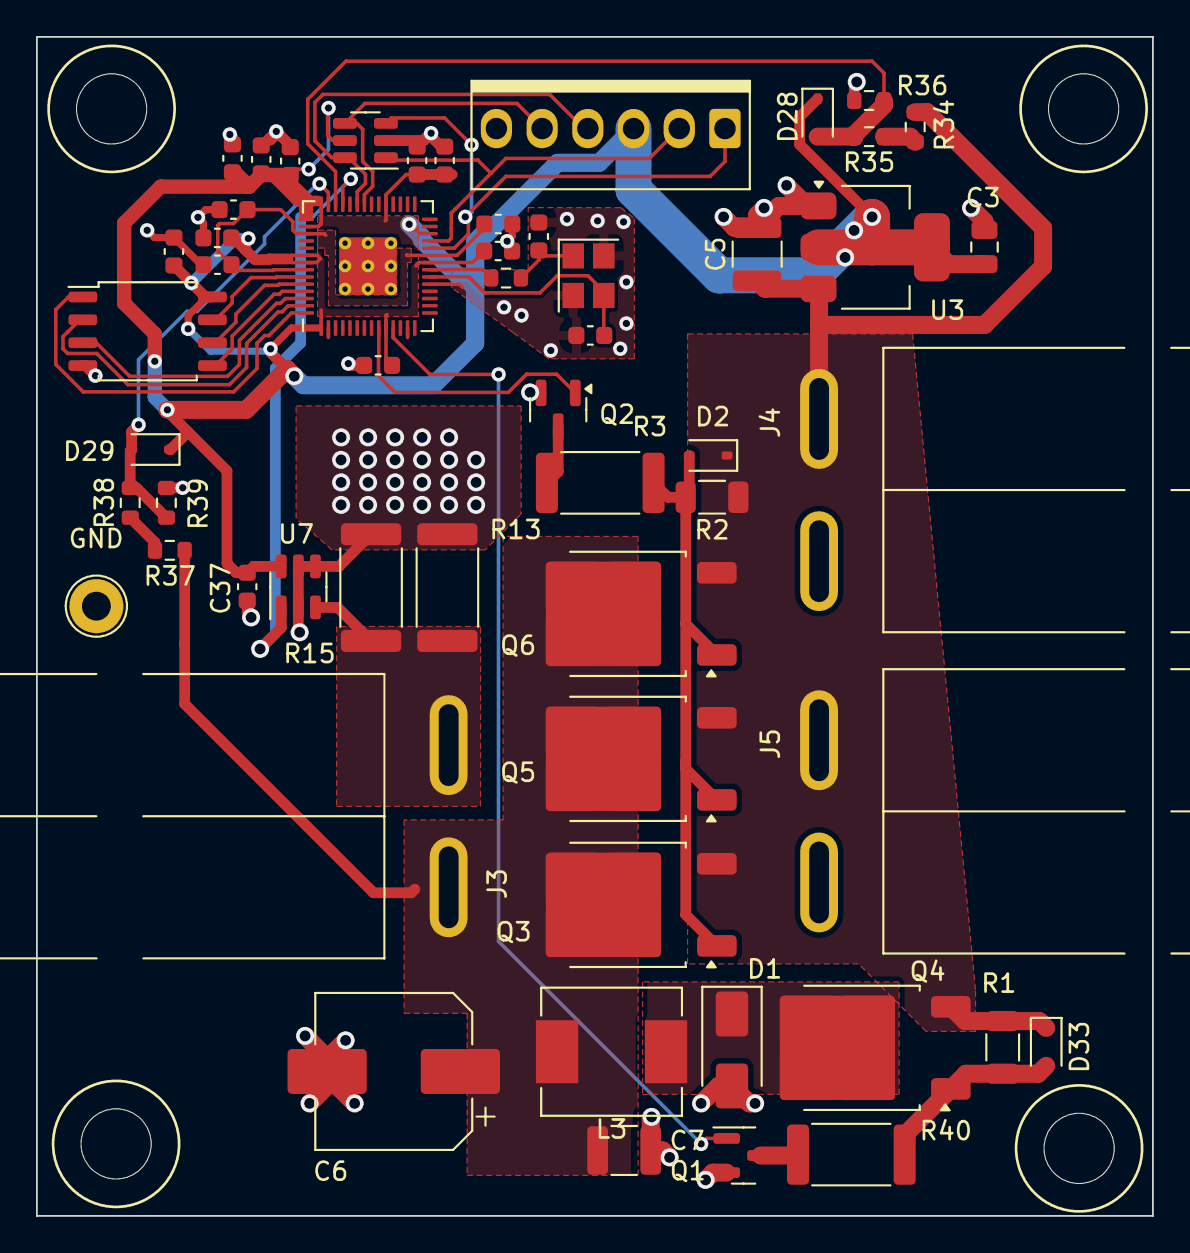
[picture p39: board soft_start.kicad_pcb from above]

Board: 4 copper layers, 62.0 x 65.5 mm, 59 parts (0 on the bottom side), 31 nets.

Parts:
C1, C2: 20p; C_0603_1608Metric
C3: 10u; C_0805_2012Metric
C4, C14, C15, C29, C30, C31, C33, C34, C35, C36, C37: 100n; C_0603_1608Metric
C5, C7: 4.7uF 100V; C_1210_3225Metric
C6: 47uF 63V solid; CP_Elec_8x10.5
C16, C32: 1u; C_0603_1608Metric
D1: SS310; D_SMA
D2, D33: Zener 10v; D_SOD-323
D28, D29: 1N4148WS; D_SOD-323
H1, H2, H3, H4: MountingHole; MountingHole_3.9mm_Plastite_#6
J2: Conn_01x06; Ckmtw-W-2510S06P_1x06_P2.54mm_Vertical
J3: Power Output; PowerPole_PP45_1336G1_1x2_Horizontal
J4, J5: Conn_01x02; PowerPole_PP45_1336G1_1x2_Horizontal
L3: 47uH; L_Chilisin_BMRB00060612
Q1, Q2: Q_NMOS_GSD; SOT-23
Q3, Q4, Q5, Q6: 100V 34A PMOS; TO-252-2
R1, R2: 10k; R_1206_3216Metric
R3, R40: 2k 2 watt; R_2512_6332Metric
R8: 1.1k; R_0603_1608Metric
R13, R15: 3mΩ; R_2512_6332Metric
R34, R35, R37, R38: 50k 0.1%; R_0603_1608Metric
R36, R39: 5.1k 0.1%; R_0603_1608Metric
TP1: TestPoint; TestPoint_Loop_D2.60mm_Drill1.6mm_Beaded
U1: USBLC6-4SC6; SOT-23-6
U2: W25Q128JVSIQ; SOIC-8_5.23x5.23mm_P1.27mm
U3: LD1117S33TR_SOT223; SOT-223-3_TabPin2
U4: RP2040; RP2040-QFN-56
U7: INA181A2; SOT-23-6
Y1: 12MHz; Crystal_SMD_3225-4Pin_3.2x2.5mm

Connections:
+3V3: C3.1, C4.1, C29.1, C30.1, C31.1, C32.1, C33.1, C34.1, C35.1, C36.1, C37.1, D28.1 (K), D29.1 (K), J2.3, U1.5 (VBUS), U2.8 (VCC), U3.2 (VO), U4.1 (IOVDD), U4.10 (IOVDD), U4.22 (IOVDD), U4.26 (RUN), U4.33 (IOVDD), U4.42 (IOVDD), U4.43 (ADC_AVDD), U4.44 (VREG_IN), U4.48 (USB_VDD), U4.49 (IOVDD), U7.6 (V+)
/1V1: C14.1, C15.1, C16.1, U4.23 (DVDD), U4.45 (VREG_VOUT), U4.50 (DVDD)
/QSPI_SCLK_2: U2.6 (CLK), U4.52 (QSPI_SCLK)
/QSPI_SD0_2: U2.5 (DI(IO0)), U4.53 (QSPI_SD0)
/QSPI_SD1_2: U2.2 (DO(IO1)), U4.55 (QSPI_SD1)
/QSPI_SD2_2: U2.3 (IO2), U4.54 (QSPI_SD2)
/QSPI_SD3_2: U2.7 (IO3), U4.51 (QSPI_SD3)
/QSPI_SS_2: U2.1 (~CS), U4.56 (QSPI_SS)
/RXI_2: J2.4, U1.6 (I/O4), U4.37 (GPIO25)
/SWCLK_2: J2.1, U1.3 (I/O2), U4.24 (SWCLK)
/SWD_2: J2.2, U1.1 (I/O1), U4.25 (SWD)
/TXO_2: J2.5, U1.4 (I/O3), U4.36 (GPIO24)
/V_OUT_P_GATE: D2.2 (A), Q3.1 (G), Q5.1 (G), Q6.1 (G), R2.2, R3.2
CURRENT_MEASURE: U4.39 (GPIO27_ADC1), U7.1
GND: C1.2, C2.2, C3.2, C4.2, C5.2, C6.2, C7.2, C14.2, C15.2, C16.2, C29.2, C30.2, C31.2, C32.2, C33.2, C34.2, C35.2, C36.2, C37.2, D1.2 (A), J2.6, J4.2, J5.2, Q1.2 (S), Q2.2 (S), R13.1, R15.1, R36.2, R39.2, TP1.1, U1.2 (GND), U2.4 (GND), U3.1 (GND), U4.19 (TESTEN), U4.57 (GND), U7.2 (GND), U7.4 (-), U7.5 (REF), Y1.2, Y1.4
unnamed: C2.1, R8.2, Y1.1
unnamed: D1.1 (K), L3.1, Q4.2 (D)
unnamed: D33.2 (A), Q4.1 (G), R1.2, R40.2
unnamed: J3.2, R13.2, R15.2, U7.3 (+)
unnamed: Q1.3 (D), R40.1
unnamed: Q2.3 (D), R3.1
unnamed: R34.2, R35.1
unnamed: R37.2, R38.1
unnamed: C1.1, U4.20 (XIN), Y1.3
unnamed: R8.1, U4.21 (XOUT)
VINPUT: C5.1, D2.1 (K), D33.1 (K), J4.1, J5.1, Q3.3 (S), Q4.3 (S), Q5.3 (S), Q6.3 (S), R1.1, R2.1, R34.1, U3.3 (VI)
VINPUT_MEASURE: D28.2 (A), R35.2, R36.1, U4.40 (GPIO28_ADC2)
VOUT: C6.1, C7.1, J3.1, L3.2, Q3.2 (D), Q5.2 (D), Q6.2 (D), R37.1
VOUT_ENABLE: Q2.1 (G), U4.9 (GPIO7)
VOUT_MEASURE: D29.2 (A), R38.2, R39.1, U4.41 (GPIO29_ADC3)
V_OUT_INDUCTOR: Q1.1 (G), U4.11 (GPIO8)

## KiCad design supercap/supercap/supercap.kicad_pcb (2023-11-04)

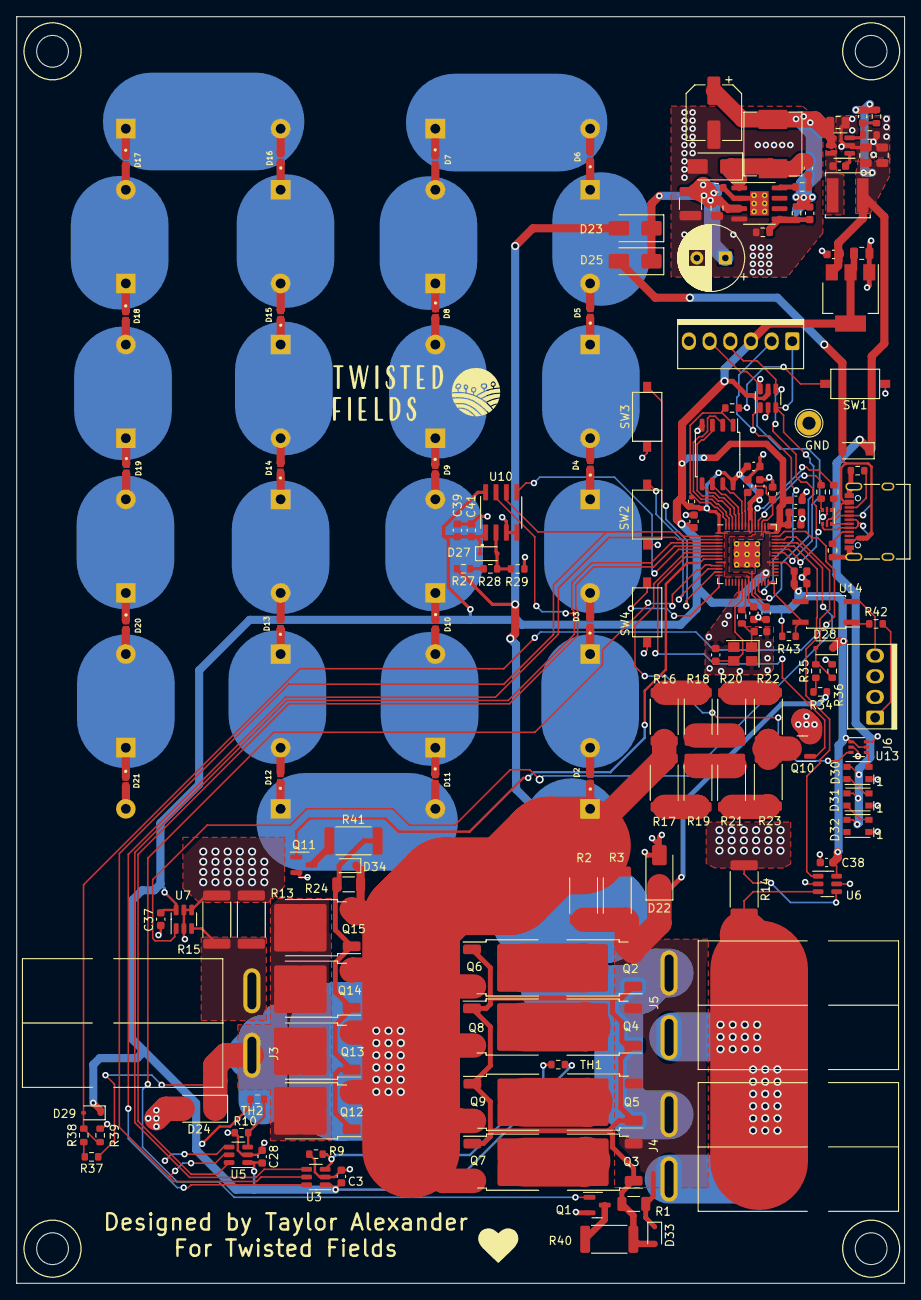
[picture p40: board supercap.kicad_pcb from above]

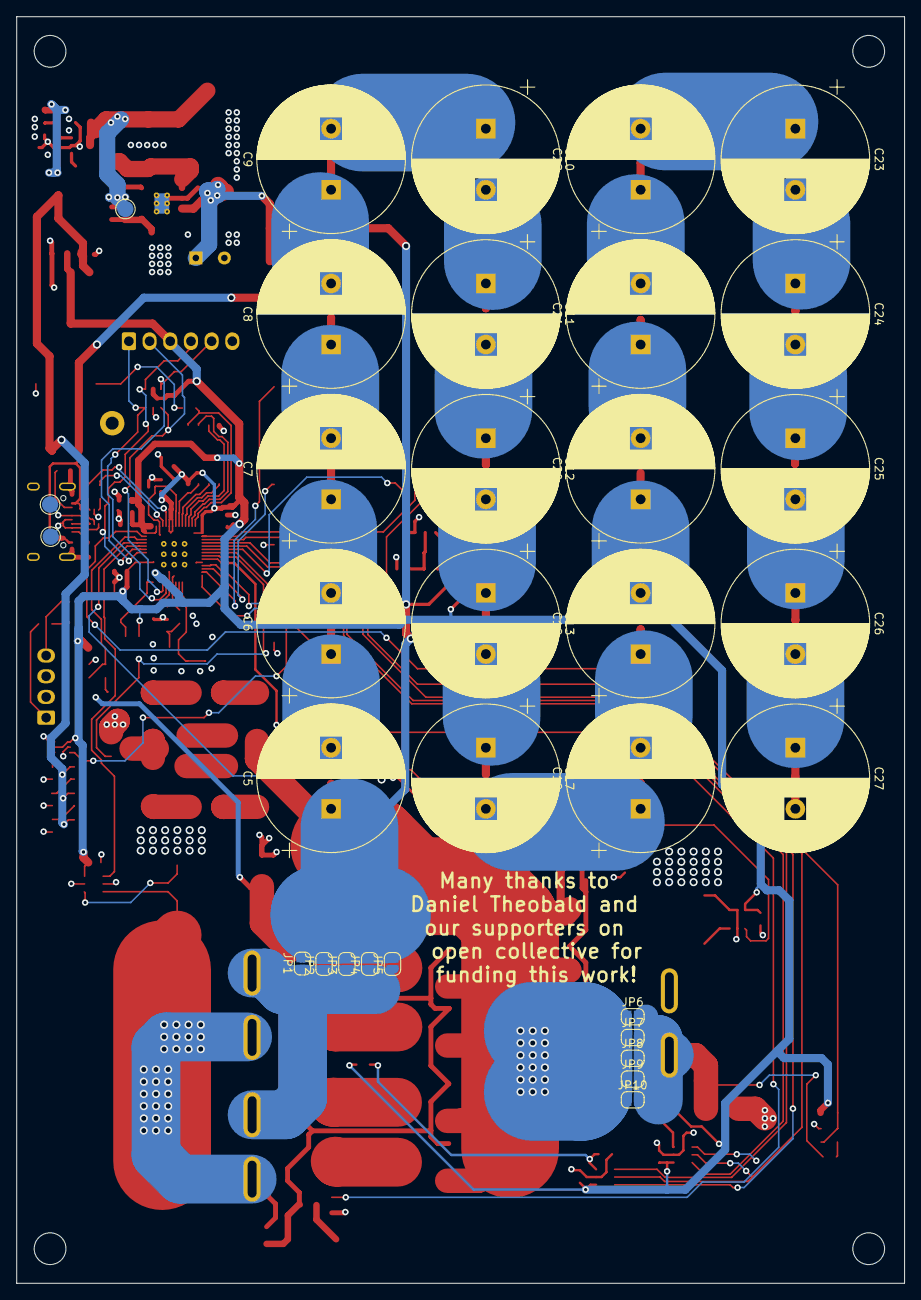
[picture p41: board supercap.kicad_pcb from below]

Board: 4 copper layers, 109.0 x 155.5 mm, 192 parts (33 on the bottom side), 105 nets.

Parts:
C1, C2: 20p; C_0603_1608Metric
C3, C16, C28, C32, C39, C45: 1u; C_0603_1608Metric
C4, C14, C15, C29, C30, C31, C33, C34, C35, C36, C37, C38, C41, C47: 100n; C_0603_1608Metric
C5, C6, C7, C8, C9, C10, C11, C12, C13, C17, C18, C19, C20, C21, C22, C23, C24, C25, C26, C27: 120F 2.3v; CP_Radial_D18.0mm_P7.50mm
C40: 47uF 63V solid; CP_Radial_D8.0mm_P3.50mm
C42, C52: 22uF 25V; C_0805_2012Metric
C43: 4.7uF 100V; C_1210_3225Metric
C44: 100nF 100V; C_0805_2012Metric
C46: 22nF; C_0603_1608Metric
C48: 10u; C_0805_2012Metric
C49: 22pF; C_0603_1608Metric
C50: 47uF 10v; C_0805_2012Metric
C51: 47pf; C_0603_1608Metric
C53: 220uF 25V; CP_Elec_6.3x7.7
D1: B5819W SL; D_SOD-123
D2, D3, D4, D5, D6, D7, D8, D9, D10, D11, D12, D13, D14, D15, D16, D17, D18, D19, D20, D21: 2.4v zener; DIO_PESD5V0S1UL_315
D22, D24: SMAJ51A; D_SMA
D23, D25: D; D_SMA
D26: SS310; D_SMA
D27, D28, D29: 1N4148WS; D_SOD-323
D30, D31, D32: WS2812B; LED_WS2812_3528_3.5x2.8mm_P1.5mm
D33, D34: Zener 10v; D_SOD-323
H1, H2, H3, H4: MountingHole; MountingHole_3.9mm_Plastite_#6
J1: CPU2 USB; USB_C_Receptacle_XKB_U262-16XN-4BVC11
J2: Conn_01x06; Ckmtw-W-2510S06P_1x06_P2.54mm_Vertical
J3: Power Output; PowerPole_PP45_1336G1_1x2_Horizontal
J4, J5: Conn_01x02; PowerPole_PP45_1336G1_1x2_Horizontal
J6: CAN2 PLUG; PINREX-744-81-04TW00 _1x04_P2.54mm_Vertical
JP1, JP2, JP3, JP4, JP5, JP6, JP7, JP8, JP9, JP10: SolderJumper_2_Open; SolderJumper-2_P1.3mm_Open_RoundedPad1.0x1.5mm
L1: 10uH; L_Sunlord_SWPA5040S
L2: 47uH; L_Chilisin_BMRB00060612
Q1, Q10, Q11: Q_NMOS_GSD; SOT-23
Q2, Q3, Q4, Q5, Q6, Q7, Q8, Q9, Q12, Q13, Q14, Q15: 100V 34A PMOS; TO-252-2
R1, R24: 10k; R_1206_3216Metric
R2, R3: 1k 2 watt; R_2512_6332Metric
R4, R8: 1.1k; R_0603_1608Metric
R5: DNS; R_0402_1005Metric
R6, R7, R43: 5.1k; R_0603_1608Metric
R9, R10: 10k; R_0603_1608Metric
R11, R12: 27; R_0603_1608Metric
R13, R14, R15: 3mΩ; R_2512_6332Metric
R16, R17, R18, R19, R20, R21, R22, R23: 100R 2W; R_2512_6332Metric
R25: 50mΩ; R_0603_1608Metric
R26: 10Ω; R_0603_1608Metric
R27, R28, R34, R35, R37, R38: 50k 0.1%; R_0603_1608Metric
R29, R36, R39: 5.1k 0.1%; R_0603_1608Metric
R30: 110k 0.1%; R_0603_1608Metric
R31: 15k 0.1%; R_0603_1608Metric
R32: 300k; R_0603_1608Metric
R33: 21.5k; R_0603_1608Metric
R40, R41: 2k 2 watt; R_2512_6332Metric
R42: 120R; R_0603_1608Metric
SW1, SW2, SW3, SW4: SW_MEC_5G; SW_TS_1101_C_W
TH1, TH2: Thermistor 10k; R_0603_1608Metric
TP1: TestPoint; TestPoint_Loop_D2.60mm_Drill1.6mm_Beaded
TP2, TP3, TP4: TestPoint; TestPoint_Pad_D2.0mm
U1: USBLC6-4SC6; SOT-23-6
U2: W25Q128JVSIQ; SOIC-8_5.23x5.23mm_P1.27mm
U3, U5: ADC081S021CISD/NOPB; SOT-23-6
U4: RP2040; RP2040-QFN-56
U6, U7: INA181A2; SOT-23-6
U8: USBLC6-2P6; SOT-666
U9: MT2492; SOT-23-6
U10: ADS7822U; SOIC127P599X175-8N
U11: TX4139; SOIC-8-1EP_3.9x4.9mm_P1.27mm_EP2.29x3mm_ThermalVias
U12: TLV1117LV33DCYR; SOT-223-3_TabPin2
U13: TXS0101DCKR; SOT-363_SC-70-6
U14: EL357N(C)(TA)-G; SO-4_4.4x3.6mm_P2.54mm
Y1: 12MHz; Crystal_SMD_3225-4Pin_3.2x2.5mm

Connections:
5V_ISO_PRESENT: R43.2, U4.28 (GPIO17), U14.4
+3V3: C3.2, C4.1, C28.2, C29.1, C30.1, C31.1, C32.1, C33.1, C34.1, C35.1, C36.1, C37.1, C38.1, C39.2, C41.1, C48.1, D27.1 (K), D28.1 (K), D29.1 (K), J2.3, R5.1, R43.1, TH1.1, TH2.1, U1.5 (VBUS), U2.8 (VCC), U3.1 (VA), U4.1 (IOVDD), U4.10 (IOVDD), U4.22 (IOVDD), U4.26 (RUN), U4.33 (IOVDD), U4.42 (IOVDD), U4.43 (ADC_AVDD), U4.44 (VREG_IN), U4.48 (USB_VDD), U4.49 (IOVDD), U5.1 (VA), U6.6 (V+), U7.6 (V+), U10.1 (VREF), U10.8 (+VCC), U12.2 (VO), U13.1 (VCCA), U13.5 (OE)
+5V: C45.1, C49.1, C50.2, C52.2, D1.1 (K), D30.3 (VDD), D31.3 (VDD), D32.3 (VDD), L1.2, R30.2, U12.3 (VI), U13.6 (VCCB)
+5V_ISO: J6.1, R42.1
+12V: C42.1, C51.1, C53.1, L2.2, R32.2, TP4.1, U9.4 (EN), U9.5 (IN)
/1V1: C14.1, C15.1, C16.1, U4.23 (DVDD), U4.45 (VREG_VOUT), U4.50 (DVDD)
/ADC_CLK: U3.4 (SCLK), U4.4 (GPIO2), U5.4 (SCLK), U10.7 (DCLK)
/ADC_CS1: U3.6 (~CS), U4.3 (GPIO1)
/ADC_CS2: U4.5 (GPIO3), U5.6 (~CS)
/ADC_CS3: U4.6 (GPIO4), U10.5 (~CS/SHDN)
/ADC_DATA: U3.5 (SDATA), U4.2 (GPIO0), U5.5 (SDATA), U10.6 (DOUT)
/BS: R26.1, U11.8 (BS)
/FB: C51.2, R32.1, R33.2, U11.5 (FB)
/LED: U4.7 (GPIO5), U13.3 (A)
/QSPI_SCLK_2: U2.6 (CLK), U4.52 (QSPI_SCLK)
/QSPI_SD0_2: U2.5 (DI(IO0)), U4.53 (QSPI_SD0)
/QSPI_SD1_2: U2.2 (DO(IO1)), U4.55 (QSPI_SD1)
/QSPI_SD2_2: U2.3 (IO2), U4.54 (QSPI_SD2)
/QSPI_SD3_2: U2.7 (IO3), U4.51 (QSPI_SD3)
/QSPI_SS_2: R4.1, R5.2, U2.1 (~CS), U4.56 (QSPI_SS)
/RXI_2: J2.4, U1.4 (I/O3), U4.37 (GPIO25)
/SW: C47.1, D26.1 (K), L2.1, U11.1 (SW)
/SWCLK_2: J2.1, U1.3 (I/O2), U4.24 (SWCLK)
/SWD_2: J2.2, U1.1 (I/O1), U4.25 (SWD)
/TXO_2: J2.5, U1.6 (I/O4), U4.36 (GPIO24)
/USB_DN_2: R12.2, U4.46 (USB_DM)
/USB_DP_2: R11.2, U4.47 (USB_DP)
/USB_D_2+: J1.A6 (D+), J1.B6 (D+), TP3.1, U8.6 (I/O1)
/USB_D_2-: J1.A7 (D-), J1.B7 (D-), TP2.1, U8.4 (I/O2)
/VCAP_GATE: D34.2 (A), Q12.1 (G), Q13.1 (G), Q14.1 (G), Q15.1 (G), R24.2, R41.2
/VINPUT_GATE: D33.2 (A), Q2.1 (G), Q3.1 (G), Q4.1 (G), Q5.1 (G), Q6.1 (G), Q7.1 (G), Q8.1 (G), Q9.1 (G), R1.2, R40.2
/~USB_BOOT_2: R4.2, SW1.2
BLEED_FET: Q10.1 (G), U4.8 (GPIO6)
CURRENT_MEASURE_IN: U4.38 (GPIO26_ADC0), U6.1
CURRENT_MEASURE_OUT: U4.39 (GPIO27_ADC1), U7.1
GND: C1.2, C2.2, C3.1, C4.2, C14.2, C15.2, C16.2, C27.2, C28.1, C29.2, C30.2, C31.2, C32.2, C33.2, C34.2, C35.2, C36.2, C37.2, C38.2, C39.1, C40.2, C41.2, C42.2, C43.2, C44.2, C45.2, C48.2, C50.1, C52.1, C53.2, D21.2 (A), D22.2 (A2), D24.2 (A2), D26.2 (A), D30.1 (GND), D31.1 (GND), D32.1 (GND), J1.A1 (GND), J1.A12 (GND), J1.B1 (GND), J1.B12 (GND), J1.S1 (SHIELD), J2.6, Q1.2 (S), Q10.2 (S), Q11.2 (S), R6.1, R7.2, R9.2, R10.2, R13.1, R14.1, R15.1, R29.2, R31.2, R33.1, R36.2, R39.2, SW1.1, SW2.2, SW3.2, SW4.2, TP1.1, U1.2 (GND), U2.4 (GND), U3.2 (GND), U4.19 (TESTEN), U4.57 (GND), U5.2 (GND), U6.2 (GND), U6.4 (-), U6.5 (REF), U7.2 (GND), U7.4 (-), U7.5 (REF), U8.2 (GND), U9.2 (GND), U10.3 (IN-), U10.4 (GND), U11.4 (GND), U12.1 (GND), U13.2 (GND), U14.3, Y1.2, Y1.4
GND_ISO: J6.4, U14.2
unnamed: C2.1, R8.2, Y1.1
unnamed: C47.2, R26.2
unnamed: C5.2, C6.1, D2.2 (A), D3.1 (K)
unnamed: C6.2, C7.1, D3.2 (A), D4.1 (K)
unnamed: C7.2, C8.1, D4.2 (A), D5.1 (K)
unnamed: C8.2, C9.1, D5.2 (A), D6.1 (K)
unnamed: C9.2, C10.1, D6.2 (A), D7.1 (K)
unnamed: C10.2, C11.1, D7.2 (A), D8.1 (K)
unnamed: C11.2, C12.1, D8.2 (A), D9.1 (K)
unnamed: C13.2, C17.1, D10.2 (A), D11.1 (K)
unnamed: C12.2, C13.1, D9.2 (A), D10.1 (K)
unnamed: C17.2, C18.1, D11.2 (A), D12.1 (K)
unnamed: C18.2, C19.1, D12.2 (A), D13.1 (K)
unnamed: C19.2, C20.1, D13.2 (A), D14.1 (K)
unnamed: C20.2, C21.1, D14.2 (A), D15.1 (K)
unnamed: C21.2, C22.1, D15.2 (A), D16.1 (K)
unnamed: C22.2, C23.1, D16.2 (A), D17.1 (K)
unnamed: C23.2, C24.1, D17.2 (A), D18.1 (K)
unnamed: C24.2, C25.1, D18.2 (A), D19.1 (K)
unnamed: C25.2, C26.1, D19.2 (A), D20.1 (K)
unnamed: C26.2, C27.1, D20.2 (A), D21.1 (K)
unnamed: C40.1, C43.1, C44.1, D23.1 (K), D25.1 (K), R25.2, U11.3 (VIN)
unnamed: D27.2 (A), R28.2, R29.1, U10.2 (IN+)
unnamed: D30.2 (DIN), U13.4 (B)
unnamed: D30.4 (DOUT), D31.2 (DIN)
unnamed: D31.4 (DOUT), D32.2 (DIN)
unnamed: J1.A5 (CC1), R6.2
unnamed: J1.B5 (CC2), R7.1
unnamed: J3.2, R13.2, R15.2, U7.3 (+)
unnamed: J4.2, J5.2, R14.2, U6.3 (+)
unnamed: Q1.3 (D), R40.1
unnamed: Q2.2 (D), Q6.2 (D)
unnamed: Q3.2 (D), Q7.2 (D)
unnamed: Q4.2 (D), Q8.2 (D)
unnamed: Q5.2 (D), Q9.2 (D)
unnamed: Q10.3 (D), R22.2, R23.2
unnamed: Q11.3 (D), R41.1
unnamed: R11.1, U8.1 (I/O1)
unnamed: R12.1, U8.3 (I/O2)
unnamed: R16.2, R18.1
unnamed: R17.2, R19.1
unnamed: R18.2, R20.1
unnamed: R19.2, R21.1
unnamed: R20.2, R22.1
unnamed: R21.2, R23.1
unnamed: R25.1, U11.2 (ILIM), U11.9 (ILIM)
unnamed: R27.2, R28.1
unnamed: R34.2, R35.1
unnamed: R37.2, R38.1
unnamed: R42.2, U14.1
unnamed: R9.1, TH1.2, U3.3 (VIN)
unnamed: SW2.1, U4.12 (GPIO9)
unnamed: SW3.1, U4.13 (GPIO10)
unnamed: SW4.1, U4.14 (GPIO11)
unnamed: C1.1, U4.20 (XIN), Y1.3
unnamed: R8.1, U4.21 (XOUT)
unnamed: R10.1, TH2.2, U5.3 (VIN)
unnamed: C46.1, U9.1 (BS)
unnamed: C49.2, R30.1, R31.1, U9.3 (FB)
unnamed: C46.2, L1.1, U9.6 (SW)
VBUS: D1.2 (A), D25.2 (A), J1.A4 (VBUS), J1.A9 (VBUS), J1.B4 (VBUS), J1.B9 (VBUS), U8.5 (VBUS)
VCAP: C5.1, D2.1 (K), D23.2 (A), D34.1 (K), JP1.2 (B), JP2.2 (B), JP3.2 (B), JP4.2 (B), JP5.2 (B), JP6.1 (A), JP7.1 (A), JP8.1 (A), JP9.1 (A), JP10.1 (A), Q6.3 (S), Q7.3 (S), Q8.3 (S), Q9.3 (S), Q12.3 (S), Q13.3 (S), Q14.3 (S), Q15.3 (S), R2.2, R3.2, R16.1, R17.1, R24.1, R27.1
VINPUT: D22.1 (A1), D33.1 (K), J4.1, J5.1, JP1.1 (A), JP2.1 (A), JP3.1 (A), JP4.1 (A), JP5.1 (A), Q2.3 (S), Q3.3 (S), Q4.3 (S), Q5.3 (S), R1.1, R2.1, R3.1, R34.1
VINPUT_MEASURE: D28.2 (A), R35.2, R36.1, U4.40 (GPIO28_ADC2)
VIN_ENABLE: Q1.1 (G), U4.11 (GPIO8)
VOUT: D24.1 (A1), J3.1, JP6.2 (B), JP7.2 (B), JP8.2 (B), JP9.2 (B), JP10.2 (B), Q12.2 (D), Q13.2 (D), Q14.2 (D), Q15.2 (D), R37.1
VOUT_ENABLE: Q11.1 (G), U4.9 (GPIO7)
VOUT_MEASURE: D29.2 (A), R38.2, R39.1, U4.41 (GPIO29_ADC3)

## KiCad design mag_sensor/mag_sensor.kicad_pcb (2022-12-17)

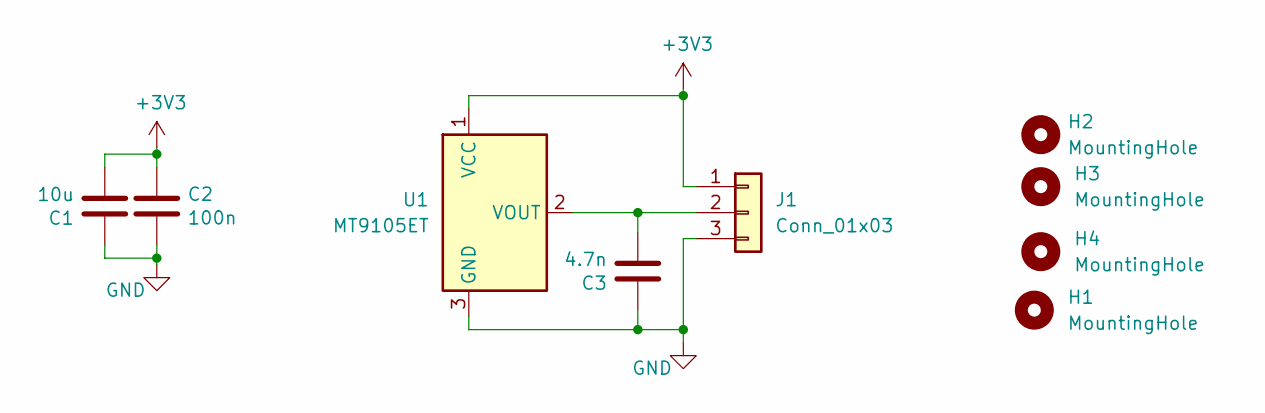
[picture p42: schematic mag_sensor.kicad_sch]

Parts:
C1: 10u; C_0805_2012Metric; LCSC C15850
C2: 100n; C_0603_1608Metric; LCSC C14663
C3: 4.7n; C_0603_1608Metric; LCSC C106218
H1, H2, H3, H4: MountingHole; MountingHole_3.9mm_Plastite_#6
J1: Conn_01x03; Molex_KK-254_AE-6410-03A_1x03_P2.54mm_Vertical; LCSC C29275
U1: MT9105ET; SOT-23; LCSC C967861

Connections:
+3V3: C1.2, C2.1, J1.1, U1.1 (VCC)
GND: C1.1, C2.2, C3.1, J1.3, U1.3 (GND)
unnamed: C3.2, J1.2, U1.2 (VOUT)


Board: 2 copper layers, 36.0 x 22.0 mm, 9 parts (1 on the bottom side), 3 nets.

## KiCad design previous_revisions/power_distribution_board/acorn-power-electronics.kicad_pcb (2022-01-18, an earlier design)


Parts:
C1, C4: 0.1uF; C_0805_2012Metric; Digikey 311-1361-1-ND
C2: 1000pF; C_0805_2012Metric; Digikey 311-1469-1-ND
C3: 0.15uF; C_0805_2012Metric; Digikey 311-3393-1-ND
D1, D2: BZX84Cxx; D_SOT-23_ANK; MPN MMBZ5240B-7-F; Digikey MMBZ5240B-FDICT-ND
H1, H2, H3, H4: MountingHole; MountingHole_3.7mm
J1: Conn_01x04; Molex_KK-254_AE-6410-04A_1x04_P2.54mm_Vertical; MPN 0022232041; Digikey WM4202-ND
J2: Conn_01x02; medium_big_pads
J3, J4, J5, J6: Conn_01x02; BigWirePads
J7: Conn_02x10_Counter_Clockwise; PinHeader_2x10_P2.54mm_Vertical; MPN SFH11-PBPC-D10-ST-BK; Digikey S9197-ND
J8: Conn_01x02; PinHeader_1x02_P2.54mm_Vertical
Q1, Q2, Q3, Q4: IXTA96P085T-TRL; TO-263-2-pad4; MPN IXTA96P085T-TRL; Digikey IXTA96P085T-TRLCT-ND
R1, R2: 330R; R_0805_2012Metric; Digikey A106061CT-ND
R3, R5: 200; R_0805_2012Metric; Digikey 311-200ARCT-ND
R4, R8: 1k; R_0805_2012Metric; MPN RC0805FR-071KL; Digikey 311-1.0KARCT-ND
R6: 1k; R_0805_2012Metric; Digikey 311-1.0KARCT-ND
R7: DNS for ACS725 / 0R for ACS722; R_0805_2012Metric; Digikey 311-0.0ARCT-ND
U1, U2: ACPL-214-500E; SOP-4_4.4x2.6mm_P1.27mm; MPN PS2805A-1-A; Digikey 559-1105-ND
U3: ACS725xLCTR-10AU; SOIC-8_3.9x4.9mm_P1.27mm; MPN ACS724LLCTR-10AB-T; Digikey 620-1719-1-ND
U4: PDS1-S5-S12-M-TR; CONV_PDS1-S3-S3-M; MPN PDS1-S5-S12-M-TR; Digikey 102-2686-1-ND
U5: ADS1115IDGS; TSSOP-10_3x3mm_P0.5mm; MPN ADS1014IDGST; Digikey 296-25226-1-ND

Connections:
+3V3: C1.2, C4.2, J7.9, J7.10, R7.1, U3.8 (VCC), U5.8 (VDD)
+5V: J7.7, J7.8, U4.2 (VIN)
+12V: J7.5, J7.6, J8.1, U4.5 (+VO)
+48V: D1.1 (K), D2.1 (K), J3.2, J7.1, J7.2, Q1.3 (S), Q2.3 (S), Q3.3 (S), Q4.3 (S), R4.2, R8.2, U3.3 (IP-), U3.4 (IP-)
A1: R6.1, U5.4 (AIN0)
A2: U5.5 (AIN1)
A3: U5.6 (AIN2)
A4: U5.7 (AIN3)
EXT_PSU_FET: J7.20, R2.1
GND: C1.1, C2.1, C3.2, C4.1, J7.11, J7.12, J8.2, U1.2, U2.2, U3.5 (GND), U4.1 (GND), U4.4 (0V), U5.1 (ADDR), U5.3 (GND)
GNDPWR: J1.3, J1.4, J2.2, J3.1, J4.1, J5.1, J6.1, J7.13, J7.14, R3.1, R5.1
unnamed: C2.2, R7.2, U3.6 (FILTER)
unnamed: C3.1, R6.2, U3.7 (VIOUT)
unnamed: D1.2 (A), Q1.1 (G), R4.1, U2.4
unnamed: R1.2, U1.1
unnamed: R2.2, U2.1
unnamed: R3.2, U1.3
unnamed: R5.2, U2.3
SCL: J7.19, U5.10 (SCL)
SDA: J7.17, U5.9 (SDA)
SOLARIN: J6.2, U3.1 (IP+), U3.2 (IP+)
VOUT: J4.2, J5.2, J7.3, J7.4, Q2.4 (D), Q3.4 (D), Q4.4 (D)
VOUT_ENABLE: J7.15, R1.1
VOUT_EXT_COMPUTE: J1.1, J1.2, J2.1, Q1.4 (D)
VOUT_FET: D2.2 (A), Q2.1 (G), Q3.1 (G), Q4.1 (G), R8.1, U1.4

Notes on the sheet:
I2C Address: 0x48


Board: 2 copper layers, 71.2 x 59.0 mm, 35 parts (0 on the bottom side), 22 nets.

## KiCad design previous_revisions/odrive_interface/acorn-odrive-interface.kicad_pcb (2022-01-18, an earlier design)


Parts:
C1, C7, C8, C10, C11: 0.1uF; C_0805_2012Metric; Digikey 311-1361-1-ND
C2, C9: 10uF; C_Elec_5x5.4; Digikey 732-8487-1-ND
C3, C4: DNP; C_0805_2012Metric
C5, C6: 3900pF NP0; C_0805_2012Metric; Digikey 490-6387-1-ND
C91, C92, C93, C94, C95, C96: 47pF; C_0805_2012Metric; Digikey 720-VJ0805A470GXJPW1BCCT-ND
D1, D2: D; D_1206_3216Metric; Digikey 641-1645-1-ND
D4, D5: CDSOT23-SM712; SOT-23-3; MPN CDSOT23-SM712; Digikey CDSOT23-SM712CT-ND
H1, H2, H3, H4, H5, H91, H92, H93, H94: MountingHole; MountingHole_3.2mm_M3
H9: MountingHole; MountingHole_6.4mm_M6
J1: Conn_01x20_Male; PinHeader_1x20_P2.54mm_Vertical; Digikey 900-0022284205-ND
J2: DNP; Molex_KK-254_AE-6410-02A_1x02_P2.54mm_Vertical; Digikey 900-0022232021-ND
J3: DNP; Molex_KK-396_A-41791-0003_1x03_P3.96mm_Vertical
J4: Conn_01x02; PinHeader_1x02_P2.54mm_Vertical
J5, J6, J9, J10: Conn_01x03; Molex_KK-254_AE-6410-03A_1x03_P2.54mm_Vertical; Digikey WM4201-ND
J7: Conn_01x02; Molex_KK-254_AE-6410-02A_1x02_P2.54mm_Vertical; Digikey 900-0022232021-ND
J15: Conn_01x05; Molex_KK-254_AE-6410-05A_1x05_P2.54mm_Vertical; Digikey WM2703-ND
J16: RJ45_LED_Shielded; RJ45_Amphenol_RJHSE538X; Digikey RJHSE-5381-ND
J91: Conn_01x12_Female; PinSocket_1x12_P2.54mm_Vertical; Digikey S1011EC-12-ND
J92, J93: Conn_01x05_Male; Molex_KK-254_AE-6410-05A_1x05_P2.54mm_Vertical; Digikey WM2703-ND
JP1, JP2: SolderJumper_2_Open; SolderJumper-2_P1.3mm_Open_RoundedPad1.0x1.5mm
JP91, JP92: SolderJumper_3_Bridged12; SolderJumper-3_P1.3mm_Open_RoundedPad1.0x1.5mm
Q1: DNP; SOT-23-3; MPN FDV303N; Digi-Key_PN DMN10H220L-7DICT-ND
R1: 220R; R_0805_2012Metric; Digikey A129741CT-ND
R2, R11: 10k; R_0805_2012Metric; Digikey 311-10.0KCRCT-ND
R3, R4: 1M; R_0805_2012Metric; Digikey 311-1.00MCRCT-ND
R5, R7, R8, R10: 750R; R_0805_2012Metric; Digikey RMCF0805FT750RCT-ND
R6, R9: 130R; R_0805_2012Metric; Digikey RMCF0805FT130RCT-ND
R12, R13, R14: 470R; R_0805_2012Metric; Digikey RMCF0805FT470RCT-ND
R15, R16: DNP; TO-247-2_Vertical
R17: 100R; R_0805_2012Metric; Digikey 311-100CRCT-ND
TP1, TP2, TP4, TP5, TP91, TP92, TP93, TP94, TP95, TP96, TP97: TestPoint; TestPoint_Keystone_5015_Micro-Minature
U1: PS2805A-1-A; SOP-4_4.4x2.6mm_P1.27mm; Digikey 559-1105-ND
U2: THVD1451D; SOIC-8_3.9x4.9mm_P1.27mm; Digikey MAX3490EESA+CT-ND
U3, U5: buffer; SN74LVC1G07QDCKTQ1; MPN TC7SZ07FU,LJ(CT; Digikey TC7SH34FULJ(CTCT-ND
U4: UCC2946D; SO-8_3.9x4.9mm_P1.27mm; Digikey 296-2645-5-ND
U6: BV1LC105FJ-C; SOJ-8_6x4mm_P1.27mm; Digikey BV1LC105FJ-CE2CT-ND
U7, U8: 1558667-1; Digikey PB2398-ND

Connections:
3v3: C7.1, C8.1, C10.1, C11.1, J1.1, J4.2, J9.2, J10.2, J16.10, J16.12, J91.1, J91.7, JP91.1 (A), JP92.1 (A), R3.2, R7.2, R8.1, TP1.1, U1.4, U2.1 (VCC), U3.5 (VCC), U4.8 (VDD), U5.5 (VCC)
5V: C2.1, C9.1, D1.1 (K), D2.1 (K), J91.2, J91.8, JP91.3 (B), JP92.3 (B), U7.4, U8.4
/Enc1PosV: J93.1, JP92.2 (C)
AGND: C3.2, C4.2, J1.7, J5.1, J6.1
AVCC: J1.6, J5.2, J6.2, TP5.1
CAN_H: J1.3
CAN_L: J1.4
COIL_DRIVE: D1.2 (A), D2.2 (A), Q1.3 (D), U6.8 (OUT1), U7.5, U8.5
E1: J2.1, J16.8, R1.1
E2: J2.2, J16.7, U1.2
E_SWITCH1: J7.1, J16.5
E_SWITCH2: J7.2, J16.4
Enc0A: C92.1, J91.9, J92.2, TP95.1
Enc0B: C94.1, J91.10, J92.3, TP96.1
Enc0Z: C96.1, J91.11, J92.4, TP97.1
Enc1A: C91.1, J91.3, J93.2, TP92.1
Enc1B: C93.1, J91.4, J93.3, TP93.1
Enc1Z: C95.1, J91.5, J93.4, TP94.1
GND: C1.1, C2.2, C5.2, C6.2, C7.2, C8.2, C9.2, C10.2, C11.2, C91.2, C92.2, C93.2, C94.2, C95.2, C96.2, D4.3 (Output), D5.3 (Output), J1.2, J1.5, J1.19, J1.20, J9.1, J10.1, J15.5, J91.6, J91.12, J92.5, J93.5, Q1.2 (S), R2.2, R4.1, R5.1, R10.1, R11.2, TP4.1, TP91.1, U2.4 (GND), U3.3 (GND), U4.1 (GND), U5.3 (GND), U6.7 (GND)
GPIO_1: J1.11, U2.3 (D), U5.2 (A)
GPIO_2: J1.12, U2.2 (R), U3.2 (A)
GPIO_3: C3.1, J1.13, J5.3
GPIO_4: C4.1, J1.14, J6.3
GPIO_5: J1.15, J9.3
GPIO_6: J1.16, J10.3
GPIO_7: J1.17, R17.2, U6.1 (IN)
GPIO_8: J1.18, J4.1, R11.1, TP2.1, U4.5 (*WDO)
unnamed: C1.2, R14.2
unnamed: C5.1, U4.4 (RP)
unnamed: C6.1, U4.6 (WP)
unnamed: D4.1 (Input), J15.2, J16.3, R9.2, R10.2, U2.6 (Z)
unnamed: D4.2 (Input), J15.1, J16.6, R8.2, R9.1, U2.5 (Y)
unnamed: D5.1 (Input), J15.4, J16.1, R6.2, R7.1, U2.8 (A)
unnamed: D5.2 (Input), J15.3, J16.2, R5.2, R6.1, U2.7 (B)
unnamed: J3.1, U8.1
unnamed: J3.2, JP1.1 (A), JP2.2 (B), R15.2, R16.1
unnamed: J3.3, U7.3
unnamed: J16.9, R12.2
unnamed: J16.11, R13.2
unnamed: J16.SH, R14.1
unnamed: J92.1, JP91.2 (C)
unnamed: JP1.2 (B), R15.1, U8.3
unnamed: JP2.1 (A), R16.2, U7.1
unnamed: Q1.1 (G), R17.1
unnamed: R1.2, U1.1
unnamed: R3.1, R4.2, U4.2 (RTH)
SPI_MISO: J1.9
SPI_MOSI: J1.10
SPI_SCK: J1.8
WDI: R2.1, U1.3, U4.7 (WDI)
led_buffer_rx: R12.1, U3.4 (Y)
led_buffer_tx: R13.1, U5.4 (Y)

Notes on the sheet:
Alternative to other driver.
Design licensed CC0 - Public Domain. Use this information for any purpose. Created by Taylor Alexander for Twisted Fields Llc. Thanks to Daniel Theobald for funding the work.


Board: 2 copper layers, 138.5 x 68.2 mm, 86 parts (1 on the bottom side), 47 nets.

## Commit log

2022-01-18 Add all updated boards for V2 system refresh
    [RPi_Hat-Edge_Cuts.dxf, RPi_Hat-F_Mask.dxf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]
2022-03-01 Add photo of PCB to readme and doc folder
2022-11-24 add new JLCPCB assembled motherboard and archive old boards
    [5556416-1.stp, DWV0008A.stp, HR911105A.step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]
2022-12-17 Update latest files for CM4 robot board. Ordered this version.
    [DCK0006A.stp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]
2022-12-17 Add magnetic homing sensor design files.
    [mag_sensor-B_Cu.gbl, mag_sensor-B_Mask.gbs, mag_sensor-B_Paste.gbp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]
2023-10-13 add supercap board
    [Anderson P45_dual.step, CP_Radial_D18.0mm_P7.50mm_L60.0mm.step, capacitors.dxf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]
2023-11-04 Rev 2 Supercap PCB, updates to Motherboard in progress
    [bom.csv, cm4-robot.csv, cm4-robot.kicad_pcb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]
2023-11-18 CM4 robot board almost done for Rev 3.5
    [cm4-robot.kicad_pcb, cm4-robot.kicad_sch]
2024-01-18 Updated Motherboard design files to latest version.
    [MSAS-08PFFR-SF7003-STP.STP, cm4-robot.kicad_pcb, cm4-robot.kicad_sch]
2024-04-12 Update motherboard, in progress not complete
    [Anderson P45_dual.step, CONN-TH_5P-P2.54_HCTL_HC-2510-5AW.obj, LED-ARRAY-SMD_4P-L2.1-W2.1-TL_NH-B2020RGBA.obj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]
2024-04-26 Update motherboard and add soft start pcb
    [Anderson P45_dual.step, CP_Radial_D18.0mm_P7.50mm_L60.0mm.step, LED-ARRAY-SMD_4P-L1.9-W1.6-BL-CW.obj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]
2024-05-06 Fix motherboard schematic page size
    [cm4-robot.kicad_pcb]
2024-05-31 Motherboard: Add GPS port and other updates. Ready for review.
    [Pantalla OLED 0.96'' 128x64.stp, cm4-robot.kicad_pcb, cm4-robot.kicad_sch]
2024-05-31 remove extra schematic notes
    [cm4-robot.kicad_sch]
2024-07-11 update motherboard, add supercap_simple. ready for review
    [Anderson P45_dual.step, CP_Radial_D18.0mm_P7.50mm_L60.0mm.step, Download_STP_610108249221_rev1.stp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]
2024-07-12 move CM4 connector off board to fix DRC errors, exclude other errors as appropriate
    [cm4-robot.kicad_pcb]
2024-07-12 Resolve most of the schematic ERC errors.
    [cm4-robot.kicad_pcb, cm4-robot.kicad_sch]
2024-07-12 Clean up additional ERC warnings.
    [cm4-robot.kicad_pcb]
2024-07-13 Update with most design review feedback. Needs final checkout.
    [cm4-robot.kicad_pcb, cm4-robot.kicad_sch]
2024-08-03 Updated board files for July 2024 order. Added supercap_simple.
    [XT30PW-F.STEP, XT30PW-M--3DModel-STEP-269445.STEP, bom.csv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]

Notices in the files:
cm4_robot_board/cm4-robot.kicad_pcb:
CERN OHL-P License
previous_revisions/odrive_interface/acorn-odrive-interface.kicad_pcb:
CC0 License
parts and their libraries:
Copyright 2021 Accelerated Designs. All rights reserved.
